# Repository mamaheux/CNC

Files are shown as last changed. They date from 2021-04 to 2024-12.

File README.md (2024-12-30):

# CNC
This is a project to learn how to create a 3-axis CNC router. It contains the mechanical, electrical and software designs.

## Folder Descriptions

### CAD
This folder contains the CAD files to build the CNC. It is built from aluminium extrusions and 3D printed parts.

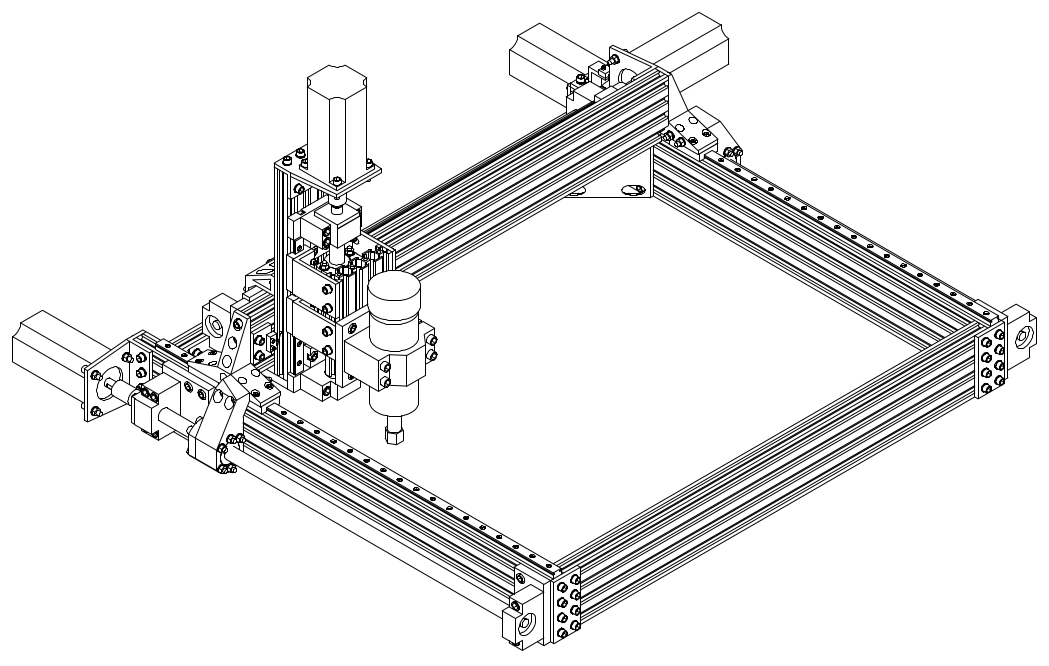
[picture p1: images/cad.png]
CAD


### control
This folder contains the graphical user interface for controlling the CNC from a computer.

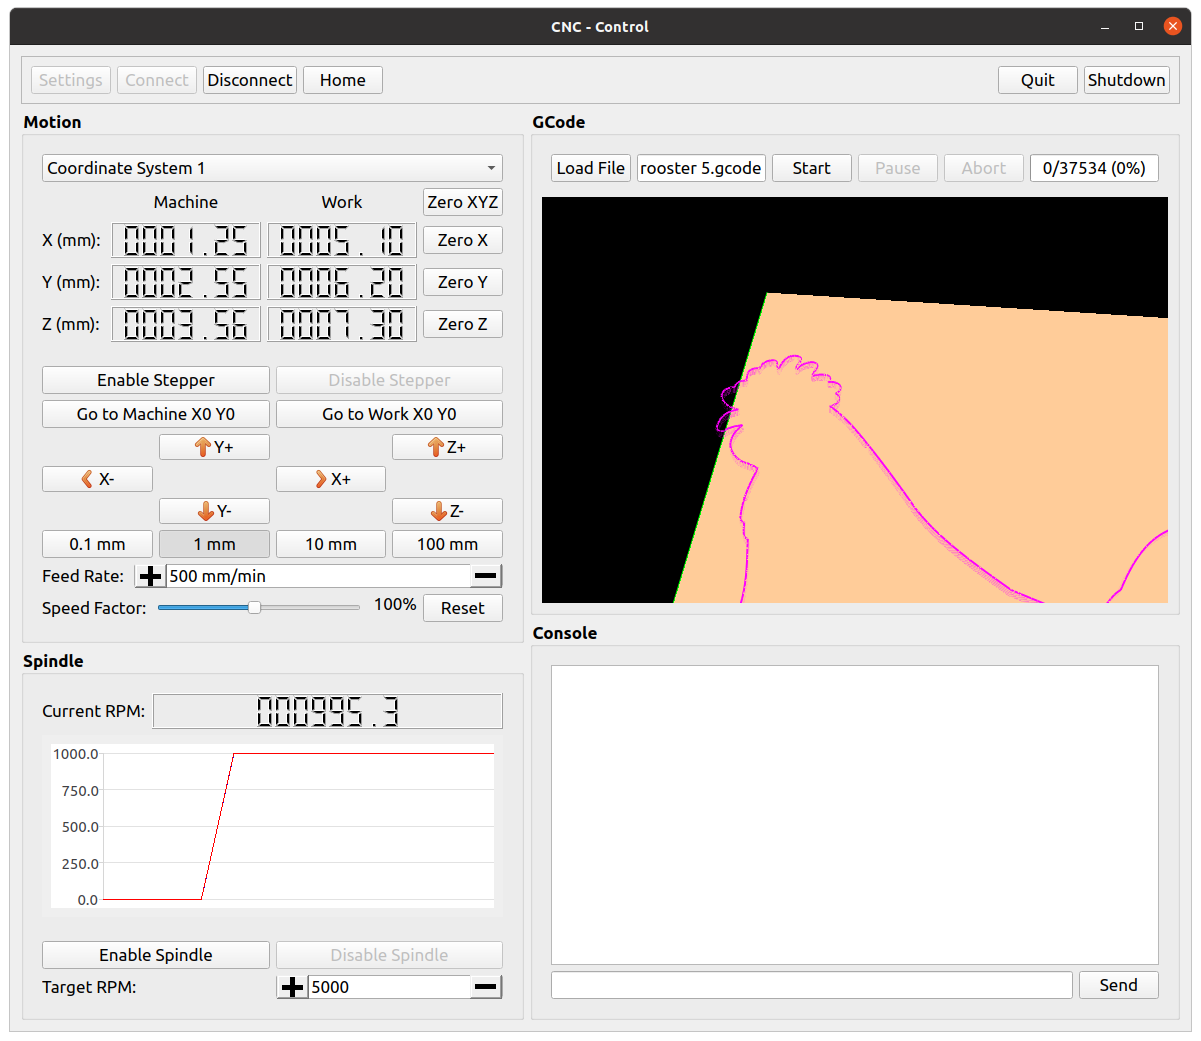
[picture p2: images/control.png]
Control


### electronics/teensy
This folder contains the PCB design of the board controlling the stepper drivers, endstops, and spindle drive.

### firmware
This folder contains the firmware that parses the G-code to control the spindle speed and the stepper motors using a trapezoidal velocity profile.

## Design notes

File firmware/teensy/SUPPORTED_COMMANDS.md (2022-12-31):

# Supported G-Codes

## G-Code Axis Names
- X
- Y
- Z
- A (not supported)
- B (not supported)
- C (not supported)
- E (not supported)
- U (not supported)
- V (not supported)
- W (not supported)

## Modal State
- Machine Coordinates
- Worskspace Coordinates (9)
- `G0` Feed Rate
- `G1`, `G2`, `G3` Feed Rate
- Global Offset (`G92`)

## Units
| Name | Units |
| --- | --- |
| Axis X, Y, Z | mm or in |
| Feedrate | mm or in per minute |
| Spindle Speed  | RPM |

## System Commands (GRBL)
| Name | Command | Handled | Tested |
| --- | --- | --- | --- |
| Homing | `$H` | Yes | Yes |

## G-Codes

| G-Code | Documentation | Parameters | Example | Handled | Tested |
| --- | --- | --- | --- | --- | --- |
| `G0` | [Link 1](https://smoothieware.org/g0), [Link 2](http://linuxcnc.org/docs/html/gcode/g-code.html#gcode:g0) | Axes, feedrate (mm/min), spindle speed | `G0 X5 F50` | Yes | Yes |
| `G1` | [Link 1](https://smoothieware.org/g1), [Link 2](http://linuxcnc.org/docs/html/gcode/g-code.html#gcode:g1) | Axes, feedrate (mm/min), spindle speed | `G1 X5 F50` | Yes | Yes |
| `G2` | [Link 1](https://smoothieware.org/g2), [Link 2](http://linuxcnc.org/docs/html/gcode/g-code.html#gcode:g2-g3) | Axes, center offsets (I, J, K) or radius (R), turn count (P), feedrate (mm/min), spindle speed | `G2 X5 Y5 I-5 J5 F10` | Yes | Yes |
| `G3` | [Link 1](https://smoothieware.org/g3), [Link 2](http://linuxcnc.org/docs/html/gcode/g-code.html#gcode:g2-g3) | Axes, center offsets (I, J, K) or radius (R), turn count (P), feedrate (mm/min), spindle speed | `G3 X5 Y5 I-5 J5 F10` | Yes | Yes |
| `G10 L2` | [Link](http://linuxcnc.org/docs/html/gcode/g-code.html#gcode:g10-l2) | Coordinate System (P), axes, R | `G10 L2 P2 X1 Y2` | Yes | Yes |
| `G10 L20`  | [Link](http://linuxcnc.org/docs/html/gcode/g-code.html#gcode:g10-l20) | Coordinate System (P), axes | `G10 L20 P3 X1` | Yes | Yes |
| `G17` | [Link 1](https://smoothieware.org/g17), [Link 2](http://linuxcnc.org/docs/html/gcode/g-code.html#gcode:g17-g19.1) | | `G17` | Yes | Yes |
| `G18` | [Link 1](https://smoothieware.org/g18), [Link 2](http://linuxcnc.org/docs/html/gcode/g-code.html#gcode:g17-g19.1) | | `G18` | Yes | Yes |
| `G19` | [Link 1](https://smoothieware.org/g19), [Link 2](http://linuxcnc.org/docs/html/gcode/g-code.html#gcode:g17-g19.1) | | `G19` | Yes | Yes |
| `G20` | [Link 1](https://smoothieware.org/g20), [Link 2](http://linuxcnc.org/docs/html/gcode/g-code.html#gcode:g20-g21) | | `G20` | Yes | Yes |
| `G21` | [Link 1](https://smoothieware.org/g21), [Link 2](http://linuxcnc.org/docs/html/gcode/g-code.html#gcode:g20-g21) | | `G21` | Yes | Yes |
| `G53` | [Link](http://linuxcnc.org/docs/html/gcode/g-code.html#gcode:g53) | G1 or G1 (modal commands are permitted) | `G53 G0 X0 Y0 Z0` | Yes | Yes |
| `G54-59.3` | [Link](http://linuxcnc.org/docs/html/gcode/g-code.html#gcode:g54-g59.3) | | `G54` | Yes | Yes |
| `G90` | [Link 1](https://smoothieware.org/g90), [Link 2](http://linuxcnc.org/docs/html/gcode/g-code.html#gcode:g90-g91) | | `G90` | Yes | Yes |
| `G90.1` | [Link 2](http://linuxcnc.org/docs/html/gcode/g-code.html#gcode:g90.1-g91.1) | | `G90.1` | Yes | Yes |
| `G91` | [Link 1](https://smoothieware.org/g91), [Link 2](http://linuxcnc.org/docs/html/gcode/g-code.html#gcode:g90-g91) | | `G91` | Yes | Yes |
| `G91.1` | [Link 2](http://linuxcnc.org/docs/html/gcode/g-code.html#gcode:g90.1-g91.1) | | `G91.1` | Yes | Yes |
| `G92` | [Link 1](https://smoothieware.org/g92), [Link 2](http://linuxcnc.org/docs/html/gcode/g-code.html#gcode:g92) | Axes (optional) | `G92 X1` | Yes | Yes |
| `G92.1` | [Link](http://linuxcnc.org/docs/html/gcode/g-code.html#gcode:g92.1-g92.2) | Axes (optional) | `G92.1` | Yes | Yes |

## Supported G-Code Parameter Names
- X
- Y
- Z
- F
- I
- J
- K
- S
- P
- R
- L

## M-Codes

| M-Code | Documentation | Parameters | Example | Handled | Tested |
| --- | --- | --- | --- | --- | --- |
| `M3` | [Link](https://smoothieware.org/m3) | Spindle Speed (S) | `M3 S500` | Yes | |
| `M5` | [Link](https://smoothieware.org/m5) | | `M5` | Yes | |
| `M17` | Enable all stepper motors. | | `M17` | Yes | Yes |
| `M18` | Disable all stepper motors. | | `M18` | Yes | Yes |
| `M20` | List all files. | | `M20` | Yes | Yes |
| `M23` | Select a G-Code file. | File path | `M23 file.gcode` | Yes | Yes |
| `M24` | Start or resume the selected file. | | `M24` | Yes | |
| `M25` | Pause the selected file. | | `M25` | Yes | |
| `M26` | Abort the selected file. | | `M26` | Yes | Yes |
| `M27` | Report the progress of the selected file (line count). | | `M27` | Yes | Yes |
| `M28` | Start to write the specified file. | File path | `M28 file.gcode` | Yes | Yes |
| `M29` | End to write the current file. | | `M29` | Yes | Yes |
| `M30` | Delete the specified file. | File path | `M30 file.gcode` | Yes | Yes |
| `M32` | Select a G-Code file and start the selected file. | File path | `M32 file.gcode` | Yes | |
| `M114` | Print the last requested position in the selected coordinate system | | `M114` | Yes | Yes |
| `M114.1` | Print the real time position in the selected coordinate system | | `M114.1` | Yes | Yes |
| `M114.2` | Print the last requested position in the machine coordinate system | | `M114.2` | Yes | Yes |
| `M114.3` | Print the real time position in the machine coordinate system | | `M114.3` | Yes | Yes |
| `M203` | Print the maximum feed rate values and set the maximum feed rate (mm/sec). | Feed rate (S) | `M203 S200` | Yes | Yes |
| `M204` | Print the acceleration values and set the acceleration (mm^2/sec). | Acceleration (S)  | `M204 S200` | Yes | Yes |
| `M220` | Print the speed factor and set the speed factor (percent). | Percent (S) | `M220 S25` | Yes | Yes |
| `M957` | Print the spindle speed (RPM) | | `M957` | Yes | Yes |
| `M958` | Print the spindle PID gain values and set the spindle PID gain values. | P, I, D | `M958 P0.1 I0.2` | Yes | Yes |

## Supported M-Code Parameter Names
- S
- File parameter
- P
- I
- D

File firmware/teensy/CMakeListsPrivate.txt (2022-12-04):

# !!! WARNING !!! AUTO-GENERATED FILE, PLEASE DO NOT MODIFY IT AND USE
# https://docs.platformio.org/page/projectconf/section_env_build.html#build-flags
#
# If you need to override existing CMake configuration or add extra,
# please create `CMakeListsUser.txt` in the root of project.
# The `CMakeListsUser.txt` will not be overwritten by PlatformIO.

set(CMAKE_CONFIGURATION_TYPES "teensy41;native;" CACHE STRING "Build Types reflect PlatformIO Environments" FORCE)

# Convert "Home Directory" that may contain unescaped backslashes on Windows

SET(CMAKE_C_COMPILER "$ENV{HOME}/.platformio/packages/toolchain-gccarmnoneeabi@1.50401.190816/bin/arm-none-eabi-gcc")
SET(CMAKE_CXX_COMPILER "$ENV{HOME}/.platformio/packages/toolchain-gccarmnoneeabi@1.50401.190816/bin/arm-none-eabi-g++")
SET(CMAKE_CXX_FLAGS "-fno-exceptions -felide-constructors -fno-rtti -std=gnu++14 -Wno-error=narrowing -fpermissive -fno-threadsafe-statics -Wall -ffunction-sections -fdata-sections -mthumb -mcpu=cortex-m7 -nostdlib -fsingle-precision-constant -mfloat-abi=hard -mfpu=fpv5-d16 -O2")
SET(CMAKE_C_FLAGS "-Wall -ffunction-sections -fdata-sections -mthumb -mcpu=cortex-m7 -nostdlib -fsingle-precision-constant -mfloat-abi=hard -mfpu=fpv5-d16 -O2")

set(CMAKE_CXX_STANDARD 14)

if (CMAKE_BUILD_TYPE MATCHES "teensy41")
    add_definitions(-DPLATFORMIO=60105)
    add_definitions(-D__IMXRT1062__)
    add_definitions(-DARDUINO_TEENSY41)
    add_definitions(-DUSB_SERIAL)
    add_definitions(-DARDUINO=10805)
    add_definitions(-DTEENSYDUINO=154)
    add_definitions(-DCORE_TEENSY)
    add_definitions(-DF_CPU=600000000)
    add_definitions(-DLAYOUT_US_ENGLISH)

    include_directories("${CMAKE_CURRENT_LIST_DIR}/include")
    include_directories("${CMAKE_CURRENT_LIST_DIR}/src")
    include_directories("${CMAKE_CURRENT_LIST_DIR}/lib/cnc/include")
    include_directories("${CMAKE_CURRENT_LIST_DIR}/lib/cnc/src")
    include_directories("$ENV{HOME}/.platformio/packages/framework-arduinoteensy/libraries/SD/src")
    include_directories("$ENV{HOME}/.platformio/packages/framework-arduinoteensy/libraries/SdFat/src")
    include_directories("$ENV{HOME}/.platformio/packages/framework-arduinoteensy/libraries/SPI")
    include_directories("${CMAKE_CURRENT_LIST_DIR}/.pio/libdeps/teensy41/optional/include")
    include_directories("${CMAKE_CURRENT_LIST_DIR}/.pio/libdeps/teensy41/optional")
    include_directories("$ENV{HOME}/.platformio/packages/framework-arduinoteensy/cores/teensy4")
    include_directories("${CMAKE_CURRENT_LIST_DIR}/.pio/libdeps/teensy41/SD")
    include_directories("$ENV{HOME}/.platformio/packages/framework-arduinoteensy/libraries/ADC")
    include_directories("$ENV{HOME}/.platformio/packages/framework-arduinoteensy/libraries/AccelStepper/src")
    include_directories("$ENV{HOME}/.platformio/packages/framework-arduinoteensy/libraries/Adafruit_NeoPixel")
    include_directories("$ENV{HOME}/.platformio/packages/framework-arduinoteensy/libraries/Adafruit_STMPE610")
    include_directories("$ENV{HOME}/.platformio/packages/framework-arduinoteensy/libraries/Adafruit_VS1053")
    include_directories("$ENV{HOME}/.platformio/packages/framework-arduinoteensy/libraries/Adafruit_nRF8001")
    include_directories("$ENV{HOME}/.platformio/packages/framework-arduinoteensy/libraries/Adafruit_nRF8001/utility")
    include_directories("$ENV{HOME}/.platformio/packages/framework-arduinoteensy/libraries/AltSoftSerial")
    include_directories("$ENV{HOME}/.platformio/packages/framework-arduinoteensy/libraries/Artnet")
    include_directories("$ENV{HOME}/.platformio/packages/framework-arduinoteensy/libraries/Audio")
    include_directories("$ENV{HOME}/.platformio/packages/framework-arduinoteensy/libraries/Audio/utility")
    include_directories("$ENV{HOME}/.platformio/packages/framework-arduinoteensy/libraries/Bounce")
    include_directories("$ENV{HOME}/.platformio/packages/framework-arduinoteensy/libraries/Bounce2/src")
    include_directories("$ENV{HOME}/.platformio/packages/framework-arduinoteensy/libraries/CapacitiveSensor")
    include_directories("$ENV{HOME}/.platformio/packages/framework-arduinoteensy/libraries/CryptoAccel/src")
    include_directories("$ENV{HOME}/.platformio/packages/framework-arduinoteensy/libraries/DS1307RTC")
    include_directories("$ENV{HOME}/.platformio/packages/framework-arduinoteensy/libraries/DmxSimple")
    include_directories("$ENV{HOME}/.platformio/packages/framework-arduinoteensy/libraries/DogLcd")
    include_directories("$ENV{HOME}/.platformio/packages/framework-arduinoteensy/libraries/EEPROM")
    include_directories("$ENV{HOME}/.platformio/packages/framework-arduinoteensy/libraries/EasyTransfer")
    include_directories("$ENV{HOME}/.platformio/packages/framework-arduinoteensy/libraries/EasyTransferI2C")
    include_directories("$ENV{HOME}/.platformio/packages/framework-arduinoteensy/libraries/Encoder")
    include_directories("$ENV{HOME}/.platformio/packages/framework-arduinoteensy/libraries/Encoder/utility")
    include_directories("$ENV{HOME}/.platformio/packages/framework-arduinoteensy/libraries/Entropy")
    include_directories("$ENV{HOME}/.platformio/packages/framework-arduinoteensy/libraries/Ethernet/src")
    include_directories("$ENV{HOME}/.platformio/packages/framework-arduinoteensy/libraries/FNET/src")
    include_directories("$ENV{HOME}/.platformio/packages/framework-arduinoteensy/libraries/FastCRC")
    include_directories("$ENV{HOME}/.platformio/packages/framework-arduinoteensy/libraries/FastLED")
    include_directories("$ENV{HOME}/.platformio/packages/framework-arduinoteensy/libraries/FlexCAN")
    include_directories("$ENV{HOME}/.platformio/packages/framework-arduinoteensy/libraries/FlexCAN_T4")
    include_directories("$ENV{HOME}/.platformio/packages/framework-arduinoteensy/libraries/FlexIO_t4/src")
    include_directories("$ENV{HOME}/.platformio/packages/framework-arduinoteensy/libraries/FlexiTimer2")
    include_directories("$ENV{HOME}/.platformio/packages/framework-arduinoteensy/libraries/FreqCount")
    include_directories("$ENV{HOME}/.platformio/packages/framework-arduinoteensy/libraries/FreqMeasure")
    include_directories("$ENV{HOME}/.platformio/packages/framework-arduinoteensy/libraries/FreqMeasureMulti")
    include_directories("$ENV{HOME}/.platformio/packages/framework-arduinoteensy/libraries/FrequencyTimer2")
    include_directories("$ENV{HOME}/.platformio/packages/framework-arduinoteensy/libraries/ILI9341_t3")
    include_directories("$ENV{HOME}/.platformio/packages/framework-arduinoteensy/libraries/ILI9488_t3/src")
    include_directories("$ENV{HOME}/.platformio/packages/framework-arduinoteensy/libraries/IRremote")
    include_directories("$ENV{HOME}/.platformio/packages/framework-arduinoteensy/libraries/Keypad/src")
    include_directories("$ENV{HOME}/.platformio/packages/framework-arduinoteensy/libraries/LedControl/src")
    include_directories("$ENV{HOME}/.platformio/packages/framework-arduinoteensy/libraries/LedDisplay")
    include_directories("$ENV{HOME}/.platformio/packages/framework-arduinoteensy/libraries/LiquidCrystal/src")
    include_directories("$ENV{HOME}/.platformio/packages/framework-arduinoteensy/libraries/LiquidCrystalFast")
    include_directories("$ENV{HOME}/.platformio/packages/framework-arduinoteensy/libraries/LittleFS/src")
    include_directories("$ENV{HOME}/.platformio/packages/framework-arduinoteensy/libraries/LowPower")
    include_directories("$ENV{HOME}/.platformio/packages/framework-arduinoteensy/libraries/MFRC522/src")
    include_directories("$ENV{HOME}/.platformio/packages/framework-arduinoteensy/libraries/MIDI/src")
    include_directories("$ENV{HOME}/.platformio/packages/framework-arduinoteensy/libraries/Metro")
    include_directories("$ENV{HOME}/.platformio/packages/framework-arduinoteensy/libraries/MsTimer2")
    include_directories("$ENV{HOME}/.platformio/packages/framework-arduinoteensy/libraries/NXPMotionSense")
    include_directories("$ENV{HOME}/.platformio/packages/framework-arduinoteensy/libraries/NXPMotionSense/utility")
    include_directories("$ENV{HOME}/.platformio/packages/framework-arduinoteensy/libraries/NativeEthernet/src")
    include_directories("$ENV{HOME}/.platformio/packages/framework-arduinoteensy/libraries/OSC")
    include_directories("$ENV{HOME}/.platformio/packages/framework-arduinoteensy/libraries/OctoWS2811")
    include_directories("$ENV{HOME}/.platformio/packages/framework-arduinoteensy/libraries/OneWire")
    include_directories("$ENV{HOME}/.platformio/packages/framework-arduinoteensy/libraries/PS2Keyboard")
    include_directories("$ENV{HOME}/.platformio/packages/framework-arduinoteensy/libraries/PS2Keyboard/utility")
    include_directories("$ENV{HOME}/.platformio/packages/framework-arduinoteensy/libraries/PWMServo")
    include_directories("$ENV{HOME}/.platformio/packages/framework-arduinoteensy/libraries/Ping")
    include_directories("$ENV{HOME}/.platformio/packages/framework-arduinoteensy/libraries/PulsePosition")
    include_directories("$ENV{HOME}/.platformio/packages/framework-arduinoteensy/libraries/QuadEncoder")
    include_directories("$ENV{HOME}/.platformio/packages/framework-arduinoteensy/libraries/RA8875")
    include_directories("$ENV{HOME}/.platformio/packages/framework-arduinoteensy/libraries/RadioHead")
    include_directories("$ENV{HOME}/.platformio/packages/framework-arduinoteensy/libraries/ResponsiveAnalogRead/src")
    include_directories("$ENV{HOME}/.platformio/packages/framework-arduinoteensy/libraries/SPIFlash")
    include_directories("$ENV{HOME}/.platformio/packages/framework-arduinoteensy/libraries/ST7735_t3")
    include_directories("$ENV{HOME}/.platformio/packages/framework-arduinoteensy/libraries/SerialFlash")
    include_directories("$ENV{HOME}/.platformio/packages/framework-arduinoteensy/libraries/Servo")
    include_directories("$ENV{HOME}/.platformio/packages/framework-arduinoteensy/libraries/ShiftPWM")
    include_directories("$ENV{HOME}/.platformio/packages/framework-arduinoteensy/libraries/Snooze/src")
    include_directories("$ENV{HOME}/.platformio/packages/framework-arduinoteensy/libraries/SoftPWM")
    include_directories("$ENV{HOME}/.platformio/packages/framework-arduinoteensy/libraries/SoftwareSerial")
    include_directories("$ENV{HOME}/.platformio/packages/framework-arduinoteensy/libraries/TFT_ILI9163C")
    include_directories("$ENV{HOME}/.platformio/packages/framework-arduinoteensy/libraries/Talkie")
    include_directories("$ENV{HOME}/.platformio/packages/framework-arduinoteensy/libraries/TeensyThreads")
    include_directories("$ENV{HOME}/.platformio/packages/framework-arduinoteensy/libraries/Time")
    include_directories("$ENV{HOME}/.platformio/packages/framework-arduinoteensy/libraries/TimeAlarms")
    include_directories("$ENV{HOME}/.platformio/packages/framework-arduinoteensy/libraries/TimerOne")
    include_directories("$ENV{HOME}/.platformio/packages/framework-arduinoteensy/libraries/TimerThree")
    include_directories("$ENV{HOME}/.platformio/packages/framework-arduinoteensy/libraries/TinyGPS")
    include_directories("$ENV{HOME}/.platformio/packages/framework-arduinoteensy/libraries/Tlc5940")
    include_directories("$ENV{HOME}/.platformio/packages/framework-arduinoteensy/libraries/TouchScreen")
    include_directories("$ENV{HOME}/.platformio/packages/framework-arduinoteensy/libraries/USBHost_t36")
    include_directories("$ENV{HOME}/.platformio/packages/framework-arduinoteensy/libraries/USBHost_t36/utility")
    include_directories("$ENV{HOME}/.platformio/packages/framework-arduinoteensy/libraries/UTFT")
    include_directories("$ENV{HOME}/.platformio/packages/framework-arduinoteensy/libraries/VirtualWire")
    include_directories("$ENV{HOME}/.platformio/packages/framework-arduinoteensy/libraries/WS2812Serial")
    include_directories("$ENV{HOME}/.platformio/packages/framework-arduinoteensy/libraries/Wire")
    include_directories("$ENV{HOME}/.platformio/packages/framework-arduinoteensy/libraries/Wire/utility")
    include_directories("$ENV{HOME}/.platformio/packages/framework-arduinoteensy/libraries/XBee")
    include_directories("$ENV{HOME}/.platformio/packages/framework-arduinoteensy/libraries/XPT2046_Touchscreen")
    include_directories("$ENV{HOME}/.platformio/packages/framework-arduinoteensy/libraries/i2c_t3")
    include_directories("$ENV{HOME}/.platformio/packages/framework-arduinoteensy/libraries/ks0108")
    include_directories("$ENV{HOME}/.platformio/packages/framework-arduinoteensy/libraries/ssd1351")
    include_directories("$ENV{HOME}/.platformio/packages/framework-arduinoteensy/libraries/x10")
    include_directories("$ENV{HOME}/.platformio/packages/toolchain-gccarmnoneeabi@1.50401.190816/arm-none-eabi/include/c++/5.4.1")
    include_directories("$ENV{HOME}/.platformio/packages/toolchain-gccarmnoneeabi@1.50401.190816/arm-none-eabi/include/c++/5.4.1/arm-none-eabi")
    include_directories("$ENV{HOME}/.platformio/packages/toolchain-gccarmnoneeabi@1.50401.190816/lib/gcc/arm-none-eabi/5.4.1/include")
    include_directories("$ENV{HOME}/.platformio/packages/toolchain-gccarmnoneeabi@1.50401.190816/lib/gcc/arm-none-eabi/5.4.1/include-fixed")
    include_directories("$ENV{HOME}/.platformio/packages/toolchain-gccarmnoneeabi@1.50401.190816/arm-none-eabi/include")

    FILE(GLOB_RECURSE EXTRA_LIB_SOURCES
        ${CMAKE_CURRENT_LIST_DIR}/.pio/libdeps/teensy41/*.*
    )
endif()

if (CMAKE_BUILD_TYPE MATCHES "native")
    add_definitions(-DPLATFORMIO=60105)

    include_directories("${CMAKE_CURRENT_LIST_DIR}/include")
    include_directories("${CMAKE_CURRENT_LIST_DIR}/src")
    include_directories("${CMAKE_CURRENT_LIST_DIR}/lib/cnc/include")
    include_directories("${CMAKE_CURRENT_LIST_DIR}/lib/cnc/src")
    include_directories("${CMAKE_CURRENT_LIST_DIR}/.pio/libdeps/native/optional/include")
    include_directories("${CMAKE_CURRENT_LIST_DIR}/.pio/libdeps/native/optional")
    include_directories("${CMAKE_CURRENT_LIST_DIR}/.pio/libdeps/native/Unity/src")

    FILE(GLOB_RECURSE EXTRA_LIB_SOURCES
        ${CMAKE_CURRENT_LIST_DIR}/.pio/libdeps/native/*.*
    )
endif()

FILE(GLOB_RECURSE SRC_LIST
    ${CMAKE_CURRENT_LIST_DIR}/src/*.*
    ${CMAKE_CURRENT_LIST_DIR}/lib/*.*
    ${CMAKE_CURRENT_LIST_DIR}/test/*.*
)

list(APPEND SRC_LIST ${EXTRA_LIB_SOURCES})

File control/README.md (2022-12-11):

# control
This is a Qt interface to control the CNC.

## Dependencies
```bash
sudo apt install qtbase5-dev qtchooser qt5-qmake qtbase5-dev-tools libqt5charts5* libqt5serialport5* libqt5opengl5* \ 
    mesa-common-dev libglu1-mesa-dev freeglut3-dev libgl-dev
```

## Linux Setup
Execute the following command `sudo visudo` and add the following line at the end.
```
%sudo ALL=(ALL) NOPASSWD: /sbin/poweroff, /sbin/reboot, /sbin/shutdown
```

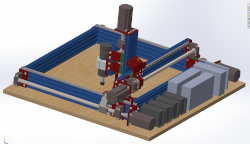
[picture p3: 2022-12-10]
control/resources/images/cnc.png

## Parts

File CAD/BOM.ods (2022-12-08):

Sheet: shop
Description | Links |  |  | Quantity
Stepper Nema 23 2.8A | ici (https://www.banggood.com/Nema-23-CNC-Stepper-Motor-DC-24-48V-3Nm-Stepper-Motor-For-CNC-Parts-p-1162662.html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) | ici (https://www.amazon.ca/-/fr/Moteur-Longueur-couple-élevé-imprimante/dp/B074W8N47K) | ici (https://www.amazon.ca/-/fr/moteurs-couple-élevé-longueur-imprimante/dp/B075KFSSP7) | 4
Stepper Driver 4.2A | ici (https://www.banggood.com/HANPOSE-DSP-Digital-DM542-128-Stepper-Motor-Driver-4_2A-DC9-42V-For-Nema-172334-Stepper-Motor-CNC-Engraving-Machine-p-1565166.html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) | ici (https://www.amazon.ca/-/fr/Pilote-moteur-phases-conduite-moteurs/dp/B07RVHVJW5?__mk_fr_CA=ÅMÅŽÕÑ&s=industrial) | ici (https://www.banggood.com/HANPOSE-TB6600-Stepper-Motor-Driver-4A-DC9-42V-For-Nema-17-or-23-or-34-Stepper-Motor-CNC-Engraving-Machine-p-1415418.html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) | 4
24V PSU | ici (https://www.banggood.com/Geekcreit-AC-110-240V-Input-To-DC-24V-17A-400W-Switching-Power-Supply-Driver-Board-p-1272112.html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) | ici (https://www.amazon.ca/Alimentation-Adaptateur-convertisseur-commutation-Transformateur/dp/B07TWW8Q73) |  | 1
Spindle + PSU + Controller | ici (https://www.banggood.com/Machifit-ER11-or-ER16-Chuck-CNC-500W-Brushless-Spindle-Motor-With-55mm-Clamps-and-Power-Supply-Speed-Governor-Speed-Control-Device-p-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) |  |  | 1
ER16 chuck collet | ici (https://www.banggood.com/ER16-10pcs-1-10mm-Spring-Collet-CNC-Carving-Machine-Milling-Chuck-Collet-Lathe-Tool-p-1199297.html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) |  |  | 1
Cable tray | ici (https://www.banggood.com/10-x-20mm-Plastic-Cable-Drag-Chain-Wire-Carrier-Length-1000mm-With-End-Connectors-For-CNC-p-995514.html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) |  |  | 2
XY ball screw | ici (https://www.banggood.com/600mm-SFU1605-Ball-Screw-with-BK12-BF12-Supports-and-6_35x10mm-Coupler-for-CNC-p-1054578.html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) |  |  | 3
Z ball screw | ici (https://www.banggood.com/SFU1605-Ball-Screw-Length-250mm-with-1-Set-BKBF12-Supports-and-6_35mm-x-10mm-Coupler-for-CNC-p-1060449.html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) |  |  | 1
X linear guide | ici (https://www.banggood.com/Machifit-MGN12-100-1000mm-Linear-Rail-Guide-with-MGN12H-Linear-Sliding-Guide-Block-CNC-Parts-p-1156260.html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) |  |  | 2
Y linear guide | ici (https://www.banggood.com/Machifit-MGN12-100-1000mm-Linear-Rail-Guide-with-MGN12H-Linear-Sliding-Guide-Block-CNC-Parts-p-1156260.html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) |  |  | 2
Z linear guide | ici (https://www.banggood.com/Machifit-MGN12-100-1000mm-Linear-Rail-Guide-with-MGN12H-Linear-Sliding-Guide-Block-CNC-Parts-p-1156260.html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) |  |  | 2
Linear guide carrier | ici (https://www.banggood.com/Machifit-MGN12H-Linear-Rail-Block-for-MGN12-Linear-Rail-Guide-CNC-Tool-p-1186173.html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) |  |  | 6
Aluminium extrusion 2080 | ici (https://www.banggood.com/Machifit-200-1000mm-Black-2080-V-Slot-Aluminum-Profile-Extrusion-Frame-for-CNC-Tool-DIY-p-1342019.html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) |  |  | 6
Controller | ici (https://www.amazon.ca/-/fr/gp/product/B082PS64QW/ref=ppx_od_dt_b_asin_title_s00?ie=UTF8&psc=1) |  |  | 1
Milling end | ici (https://www.banggood.com/Drillpro-8pcs-2-12mm-4-Flutes-Carbide-End-Mill-Set-Tungsten-Steel-Milling-Cutter-CNC-Tool-p-1139712.html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) | ici (https://www.banggood.com/7pcs-1-8mm-Solid-Carbide-Straight-End-Mill-4-Flute-Milling-Cutter-CNC-Tool-p-1665306.html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)
M2.5x10mm |  |  |  | 6
M3x8mm |  |  |  | 148
M3x25mm |  |  |  | 4
M3 T nut (50) | ici (https://www.banggood.com/Drillpro-50pcs-M3-T-Sliding-Nut-Zinc-Plated-Carbon-Steel-T-Sliding-Nut-for-2020-Aluminum-Profile-p-1081131.html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) |  |  | 3
M3 washer |  |  |  | 45
M5x10mm |  |  |  | 128
M5x20mm |  |  |  | 16
M5x30mm |  |  |  | 4
M5x50mm |  |  |  | 22
M5 T nut (100) | ici (https://www.banggood.com/Drillpro-100pcs-M5-Hammer-Nut-Nickel-Plated-Carbon-Steel-Aluminum-Connector-T-Fastener-Sliding-Nut-p-1048442.html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) |  |  | 1
M5 nut |  |  |  | 38
M5 washer |  |  |  | 170
M6x40mm |  |  |  | 24
M6x70mm |  |  |  | 4
M6 nut |  |  |  | 28
M6 washer |  |  |  | 28
Touchscreen | ici (https://www.amazon.com/13-3inch-HDMI-LCD-case-Resolution/dp/B077PTMPSX) |  |  | 1
Raspberry pi 4 | ici (https://www.buyapi.ca/product/raspberry-pi-4-model-b-4gb/) |  |  | 1

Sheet: 3D_print
File | Quantity | Printed Quantity | Total quantity | 35
spindle frame support | 4 | 4 | Printed quantity | 35
spindle mount spacer | 1 | 1
X frame BF12 spacer | 2 | 2
X frame BK12 spacer | 2 | 2
X frame corner plate | 2 | 2
X frame corner | 2 | 2
X frame screw support left | 1 | 1
X frame screw support right | 1 | 1
X limit switch support | 1 | 1
XZ frame motor support | 3 | 3
Y frame screw support | 1 | 1
Y frame support left | 1 | 1
Y frame support right | 1 | 1
Y limit switch support | 1 | 1
YZ frame BF12 spacer | 2 | 2
YZ frame BK12 spacer | 2 | 2
Z frame screw support | 1 | 1
Z frame support bottom | 1 | 1
Z frame support top | 1 | 1
Z limit switch support | 1 | 1
table support | 4 | 4

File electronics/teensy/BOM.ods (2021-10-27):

Item | Qty | Reference(s) | Value | Link
1 | 1 | C1 | 33µF/35V | https://www.digikey.ca/en/products/detail/nichicon/UPX1V330MPD1TD/4320154
2 | 1 | C2 | 10µF/10V/Low ESL | https://www.digikey.ca/en/products/detail/tdk-corporation/C2012X7R1A106M125AC/2733027
3 | 4 | C3, C9, C10, C23 | 1µF/35V | https://www.digikey.ca/en/products/detail/taiyo-yuden/GMK212BJ105KGHT/4157463
4 | 1 | C4 | 22µF/10V/Low ESL | https://www.digikey.ca/en/products/detail/tdk-corporation/C2012X5R1A226M085AC/2733098
5 | 1 | C5 | 0.33µF | https://www.digikey.ca/en/products/detail/tdk-corporation/CGA4J2X7R1H334K125AA/2443162
6 | 13 | C6, C11, C12, C13, C14, C15, C16, C17, C18, C19, C20, C22, C25 | 0.1µF/25V | https://www.digikey.ca/en/products/detail/kyocera-avx/08053C104KAT2A/1116281
7 | 1 | C7 | 330µF/10V | https://www.digikey.ca/en/products/detail/nichicon/UKL1A331MPD1TD/4318088
8 | 1 | C8 | 2.2µF/35V | https://www.digikey.ca/en/products/detail/tdk-corporation/C2012X5R1V225K085AB/3951660
9 | 1 | C21 | 47nF/21V | https://www.digikey.ca/en/products/detail/taiyo-yuden/TMK212B7473KD-T/930632
10 | 1 | C24 | 4700pF | https://www.digikey.ca/en/products/detail/samsung-electro-mechanics/CL21C472JAFNNNE/3888659
11 | 2 | D1, D2 | B340AE-13 | https://www.digikey.ca/en/products/detail/diodes-incorporated/B340AE-13/7352831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
12 | 1 | D3 | ORANGE | https://www.digikey.ca/en/products/detail/osram-opto-semiconductors-inc/LO-R976-PS-1/1227955
13 | 1 | D4 | GREEN | https://www.digikey.ca/en/products/detail/lite-on-inc/LTST-C170KGKT/386777
14 | 1 | D5 | BLUE | https://www.digikey.ca/en/products/detail/lite-on-inc/LTST-C170TBKT/388527
15 | 1 | D6 | RED | https://www.digikey.ca/en/products/detail/lite-on-inc/LTST-C171KRKT/386801
16 | 1 | J1 | Vin 24V | https://www.digikey.ca/en/products/detail/adam-tech/EBWA-02-B/9830632?s=N4IgTCBcDaIKICEDqBBAtABjGhIC6AvkA
17 | 1 | J2 | Vout 5V | Ebay – JST XH
18 | 1 | J3 | Vout 3.3V | Ebay – JST XH
19 | 1 | J4 | X_MIN | Ebay – JST XH
20 | 1 | J5 | Y_MIN | Ebay – JST XH
21 | 1 | J6 | Z_MIN | Ebay – JST XH
22 | 1 | J7 | OTHER 1 | Ebay – JST XH
23 | 1 | J8 | X_MAX | Ebay – JST XH
24 | 1 | J9 | Y_MAX | Ebay – JST XH
25 | 1 | J10 | Z_MAX | Ebay – JST XH
26 | 1 | J11 | OTHER_2 | Ebay – JST XH
27 | 3 | J12, J14, J15 | Stepper X1 | Ebay – JST XH
28 | 1 | J13 | Stepper X2 | Ebay – JST XH
29 | 2 | J16, J20 | DC Motor Vin 24V | https://www.digikey.ca/en/products/detail/adam-tech/EBWA-02-B/9830632?s=N4IgTCBcDaIKICEDqBBAtABjGhIC6AvkA
30 | 1 | J17 | Cetus_J1B1211CCD | https://www.pjrc.com/store/ethernet_kit.html
31 | 2 | J18, J21 | DC Motor | https://www.digikey.ca/en/products/detail/adam-tech/EBWA-02-B/9830632?s=N4IgTCBcDaIKICEDqBBAtABjGhIC6AvkA
32 | 1 | J22 | SPINDLE_BLDC_CONTROLLER | Ebay – JST XH
33 | 1 | J23 | USB_B | Ebay – USB-B
34 | 2 | J24, J25 | EXT | Ebay – JST XH
35 | 1 | L1 | 68µH/Sumida CDRH104R-680MC | https://www.digikey.ca/product-detail/en/sumida-america-components-inc/CDRH104RNP-680NC/308-2170-1-ND/3946461
36 | 2 | Q1, Q3 | TK1R4S04PB | https://www.digikey.ca/en/products/detail/toshiba-semiconductor-and-storage/TK1R4S04PB-LXHQ/12154999
37 | 1 | Q4 | SI2301CDS-T1-E3 | https://www.digikey.ca/en/products/detail/vishay-siliconix/SI2301CDS-T1-E3/2622018
38 | 1 | R1 | 3.01k | Ebay – Kit 0805
39 | 1 | R2 | 976 | Ebay – Kit 0805
40 | 24 | R3, R4, R5, R6, R7, R8, R9, R10, R11, R12, R13, R14, R15, R16, R17, R18, R45, R47, R48, R57, R58, R66 | 10k | https://www.digikey.ca/en/products/detail/koa-speer-electronics-inc/SG73S2ATTD103J/10279997
41 | 18 | R19, R20, R21, R22, R27, R28, R29, R30, R35, R36, R37, R38, R43, R46, R51, R55, R56, R59 | 1k | https://www.digikey.ca/en/products/detail/stackpole-electronics-inc/RNCP0805FTD1K00/2240229
42 | 12 | R23, R24, R25, R26, R31, R32, R33, R34, R39, R40, R41, R42 | 1.82k/0.5W | https://www.digikey.ca/en/products/detail/stackpole-electronics-inc/RNCP1206FTD1K82/2240344
43 | 1 | R52 | 2.2k | Ebay – Kit 0805
44 | 1 | R53 | 47k | Ebay – Kit 0805
45 | 2 | R54, R67 | 100k | Ebay – Kit 0805
46 | 2 | R60, R61 | 24 | Ebay – Kit 0805
47 | 1 | R62 | 174 | Ebay – Kit 0805
48 | 2 | R63, R65 | 150 | Ebay – Kit 0805
49 | 1 | R64 | 30.1 | Ebay – Kit 0805
50 | 1 | R68 | 0.1µF/25V | https://www.digikey.ca/en/products/detail/stackpole-electronics-inc/RMCF1206ZT0R00/1756906
51 | 8 | RV1, RV2, RV3, RV4, RV5, RV6, RV7, RV8 | VC080503A100DP | https://www.digikey.ca/en/products/detail/kyocera-avx/VC080503A100DP/684850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
52 | 1 | U1 | MIC4684 | Sample
53 | 1 | U2 | AP7354-33W5-7 | https://www.digikey.ca/en/products/detail/diodes-incorporated/AP7354-33W5-7/9554534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
54 | 1 | U3 | AZ1117IH-3.3TRG1 | https://www.digikey.ca/en/products/detail/diodes-incorporated/AZ1117IH-3-3TRG1/5699672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
55 | 2 | U4, U5 | SN74LVC14ADRG3 | https://www.digikey.ca/en/products/detail/texas-instruments/SN74LVC14ADRG3/2421075
56 | 9 | U6, U7, U8, U9, U10, U11, U12, U13, U15 | MOCD217R2M | https://www.digikey.ca/en/products/detail/onsemi/MOCD217R2M/402226
57 | 1 | U14 | TS912 | https://www.digikey.ca/en/products/detail/stmicroelectronics/TS912IDT/1040339
58 | 1 | U17 | CY7C64225 | https://www.digikey.ca/en/products/detail/cypress-semiconductor-corp/CY7C64225-28PVXC/3507932
59 | 1 | U18 | LM810M3-4.63 | https://www.digikey.ca/en/products/detail/texas-instruments/LM810M3-4-63-NOPB/364278
60 | 1 | U19 | Teensy_4.1 | https://www.pjrc.com/store/teensy41.html
61 | 1 | U19 | Header | https://www.digikey.ca/en/products/detail/samtec-inc/SQT-103-01-L-D/1108681

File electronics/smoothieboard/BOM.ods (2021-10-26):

Item | Qty | Reference(s) | Value | Link
1 | 1 | C1 | 4700pF | https://www.digikey.ca/en/products/detail/samsung-electro-mechanics/CL21B472KBANNNC/3886813
2 | 4 | C2 C15, C23, C26 | 1µF/20V | https://www.digikey.ca/en/products/detail/samsung-electro-mechanics/CL21B105KBFNNNG/3894467
3 | 2 | C3, C9 | 1000µF/20V | https://www.digikey.ca/en/products/detail/rubycon/25PX1000MEFCT810X16/3134540
4 | 2 | C4, C6 | 18pF/20V | https://www.digikey.ca/en/products/detail/kemet/C0805C180M3HAC7800/7949065
5 | 1 | C7 | 2.2µF/20V | https://www.digikey.ca/en/products/detail/samsung-electro-mechanics/CL21A225KAFNNNG/3894427
6 | 2 | C8, C27 | 10µF/20V | https://www.digikey.ca/en/products/detail/murata-electronics/GRM21BC81D106KE51L/5027585
7 | 1 | C11 | 10pF/20V | https://www.digikey.ca/en/products/detail/samsung-electro-mechanics/CL21C100CBANNNC/3888219
8 | 1 | C13 | 47nF/20V | https://www.digikey.ca/en/products/detail/samsung-electro-mechanics/CL21B473KCCWPNC/5961299
9 | 14 | C5, C14, C16, C17, C18, C19, C20, C21, C22, C28, C29, C30, C31, C32, C33 | 0.1µF/20V | https://www.digikey.ca/en/products/detail/samsung-electro-mechanics/CL21B104KBCNNNC/3886661
10 | 2 | C24, C25 | 12pF/AC | https://www.digikey.ca/en/products/detail/yageo/CC0805FRNPO9BN120/5883925
11 | 3 | D1, D2, D3 | S1B-13-F | https://www.digikey.ca/en/products/detail/diodes-incorporated/S1B-13-F/725026
13 | 1 | J1 | 5V | https://www.digikey.ca/en/products/detail/adam-tech/EBWA-02-B/9830632
14 | 1 | J2 | USB_B | https://www.digikey.ca/en/products/detail/amphenol-icc-fci/61729-0010BLF/1001353
15 | 19 | J4, J6, J8, J10, J11, J12, J13, J14, J15, J16, J17, J18, J19, J21, J22, J24, J25, J26, J28, J29 | JST* | Ebay – JST
16 | 1 | J23 | JTAG | https://www.digikey.ca/en/products/detail/sullins-connector-solutions/SBH11-PBPC-D10-ST-BK/1990065
17 | 1 | J33 | MICROSD_CARD | https://www.digikey.ca/en/products/detail/hirose-electric-co-ltd/DM3D-SF/1786510
18 | 1 | J34 | ETHERNET | https://www.digikey.ca/en/products/detail/molex/0901301112/760948
19 | 1 | JP1 | 5V
20 | 3 | JP1, JP11, JP12 | Jumper_3_Open | https://www.digikey.ca/en/products/detail/sullins-connector-solutions/QPC02SXGN-RC/2618262
21 | 1 | L1 | 10 µH | https://www.digikey.ca/en/products/detail/tdk-corporation/MLZ2012M100WT000/2465153
22 | 1 | Q6 | 2N7002-7-F | https://www.digikey.ca/en/products/detail/diodes-incorporated/2N7002-7-F/717681
23 | 1 | Q8 | BSS84 | https://www.digikey.ca/en/products/detail/on-semiconductor/BSS84/244213
24 | 2 | R1, R2 | 33 | Ebay – Kit
25 | 1 | R39 | 200 | Ebay – Kit
26 | 18 | R4, R6, R8, R13, R15, R17, R22, R24, R26, R32, R33, R36, R40, R42, R44, R46, R48, R50 | 1k | Ebay – Kit
27 | 9 | R9, R10, R11, R18, R19, R20, R27, R28, R29 | 1.82k/0.5W | https://www.digikey.ca/en/products/detail/panasonic-electronic-components/ERJ-14NF1821U/383924
28 | 1 | R30 | 50k | Ebay – Kit
29 | 11 | R31, R52, R54, R55, R57, R58, R60, R61, R64, R65, R66 | 10k | https://www.digikey.ca/en/products/detail/stackpole-electronics-inc/RNCP0805FTD10K0/2240262
30 | 5 | R34, R53, R56, R62, R63 | 2.2k | Ebay – Kit
31 | 1 | R35 | 47k | Ebay – Kit
32 | 1 | R37 | 100k | Ebay – Kit
33 | 6 | R41, R43, R45, R47, R49, R51 | 5.62k | Ebay – Kit
34 | 1 | R59 | 1.5k | Ebay – Kit
35 | 1 | RV1 | B72510T0040M062 | https://www.digikey.ca/en/products/detail/epcos-tdk-electronics/B72510T0040M062/1091373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
36 | 7 | RV2, RV4, RV5, RV6, RV7, RV8, RV9 | VC080503A100DP | https://www.digikey.ca/en/products/detail/avx-corporation/VC080503A100DP/684850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
37 | 1 | RV3 | POT_10k | https://www.digikey.ca/en/products/detail/bourns-inc/PV36W103C01B00/666502
38 | 2 | SW1, SW2 | SW_Push | https://www.digikey.ca/en/products/detail/omron-electronics-inc-emc-div/B3F-1020/44059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
39 | 1 | U1 | NUP2114UCMR6T1G | https://www.digikey.ca/en/products/detail/on-semiconductor/NUP2114UCMR6T1G/1961288
40 | 7 | U2, U3, U4, U5, U6, U7, U8 | MOCD217R2M | https://www.digikey.ca/en/products/detail/on-semiconductor/MOCD217R2M/402226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
41 | 1 | U9 | TS912 | https://www.digikey.ca/en/products/detail/stmicroelectronics/TS912BIDT/1040337
42 | 1 | U10 | AP7381_SOT89 | https://www.digikey.ca/en/products/detail/diodes-incorporated/AP7381-33Y-13/7914854
43 | 1 | U11 | LM2937IMP-3.3 | https://www.digikey.ca/en/products/detail/texas-instruments/LM2937IMP-3-3/3701483
44 | 1 | U14 | LPC1769FBD100 | https://www.digikey.ca/en/products/detail/nxp-usa-inc/LPC1769FBD100K/13540940
45 | 1 | Y1 | 12MHz | https://www.digikey.ca/en/products/detail/abracon-llc/ABM3-12-000MHZ-D2Y-T/2344574

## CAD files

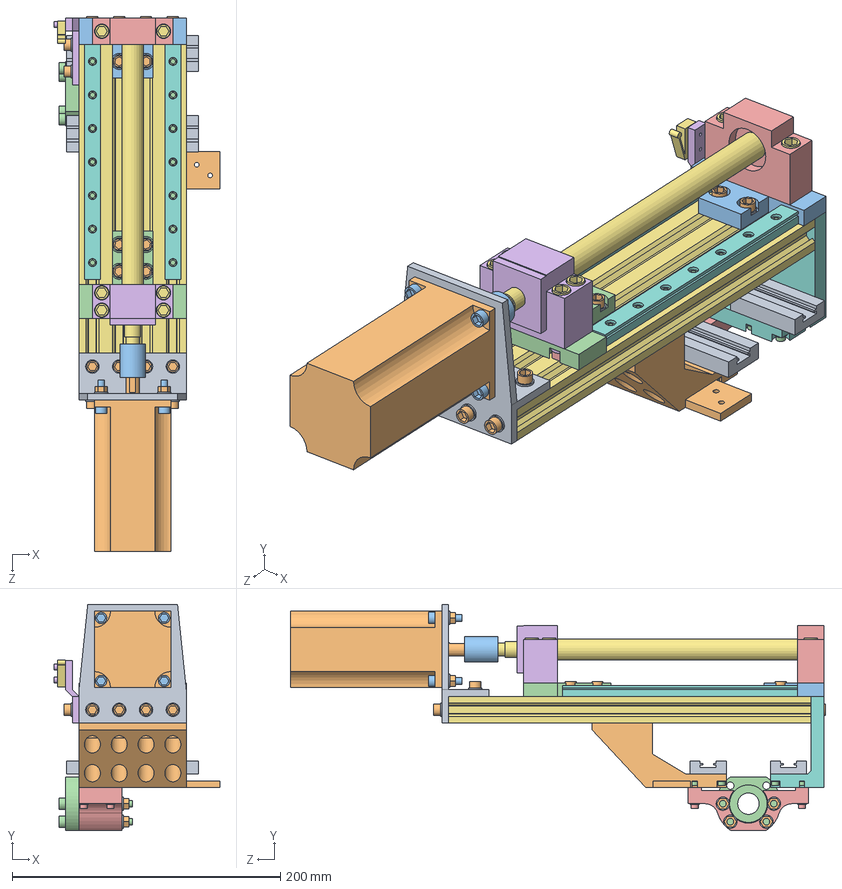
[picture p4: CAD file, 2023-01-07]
CAD/assemblies/Z frame.SLDASM
123.5 x 168.5 x 399.1 mm
M5 washer x 36
M5x10mm x 28
M3 washer x 16
M3x8mm x 26
M6 nut x 6
M6 washer x 6
M6x35mm x 6
M5 T nut x 20
M3 T nut x 14
M5 nut x 8
M5x20mm x 4
M5x50mm x 4
M3x25mm x 4
M2.5x10mm x 2
2080x270mm
Z frame support bottom
MGN12H x 4
Z frame support top
YZ frame BF12 spacer
YZ frame BK12 spacer
BF12
BK12
SFU1605x250mm
MGN12x175mm x 2
XZ frame motor support
Nema 23 3 Nm
coupler
SFU1605 nut
Y frame screw support
Z limit switch support
limit switch

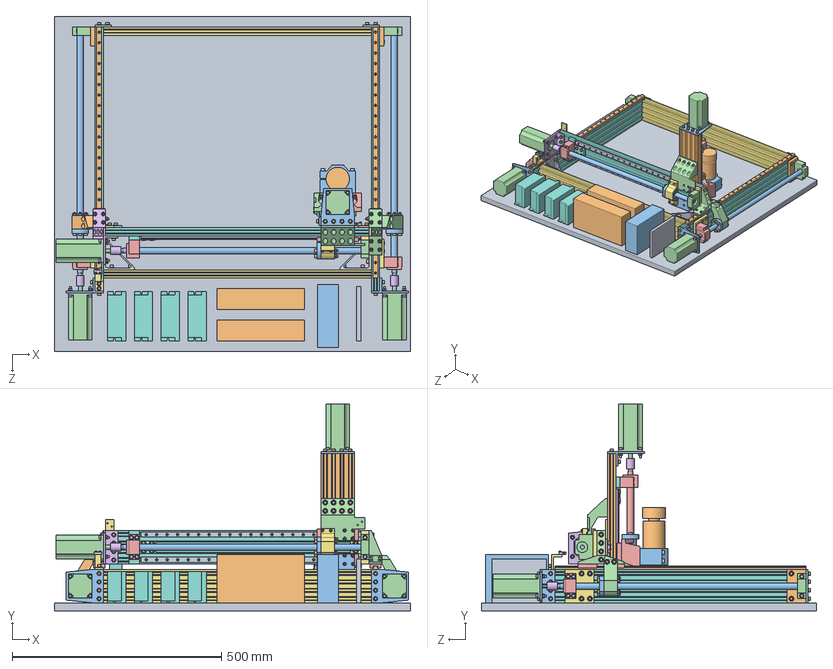
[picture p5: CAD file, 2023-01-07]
CAD/assemblies/table+CNC.SLDASM
850.0 x 493.5 x 800.0 mm
table
M5x10mm x 114
M5 washer x 156
M5 T nut x 82
M3x8mm x 140
M3 T nut x 104
2080x640mm x 2
2080x630mm x 3
X frame corner x 2
MGN12x600mm x 2
SFU1605x600mm x 3
BF12 x 4
BK12 x 4
coupler x 4
M6 nut x 28
M6 washer x 28
M6x35mm x 24
X frame BF12 spacer x 2
XZ frame motor support x 3
Nema 23 3 Nm x 4
M5 nut x 38
M5x20mm x 16
X frame BK12 spacer x 2
X frame corner plate x 2
M3 washer x 40
M5x50mm x 20
M2.5x10mm x 6
Y frame support right
MGN12H x 10
Y frame support left
YZ frame BF12 spacer x 2
YZ frame BK12 spacer x 2
MGN12x525mm x 2
X frame screw support left
SFU1605 nut x 4
X frame screw support right
Y limit switch support
limit switch x 3
Y cable tray support
X cable tray support
M3x25mm x 4
2080x270mm
Z frame support bottom
Z frame support top
SFU1605x250mm
MGN12x175mm x 2
Y frame screw support
Z limit switch support
M6x70mm x 4
spindle
spindle mount
spindle frame right
spindle frame left
M5x30mm x 2
X limit switch support
DM542 x 4
smoothieboard
PSU 24V x 2
PSU 100V

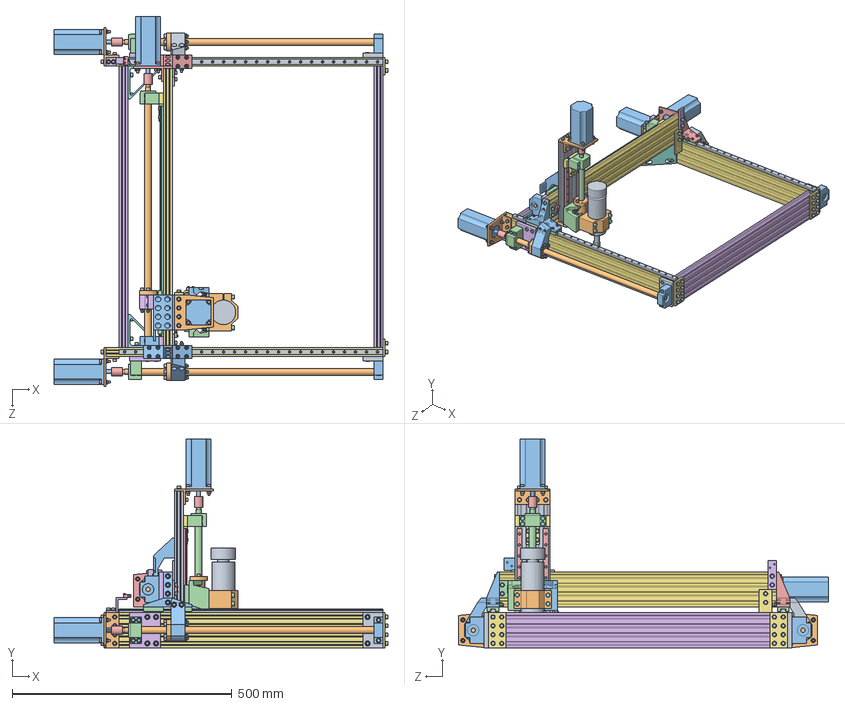
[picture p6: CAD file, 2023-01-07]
CAD/assemblies/CNC.SLDASM
759.1 x 474.5 x 841.5 mm
M5x10mm x 114
M5 washer x 156
M5 T nut x 82
M3x8mm x 140
M3 T nut x 104
2080x640mm x 2
2080x630mm x 3
X frame corner x 2
MGN12x600mm x 2
SFU1605x600mm x 3
BF12 x 4
BK12 x 4
coupler x 4
M6 nut x 28
M6 washer x 28
M6x35mm x 24
X frame BF12 spacer x 2
XZ frame motor support x 3
Nema 23 3 Nm x 4
M5 nut x 38
M5x20mm x 16
X frame BK12 spacer x 2
X frame corner plate x 2
M3 washer x 40
M5x50mm x 20
M2.5x10mm x 6
Y frame support right
MGN12H x 10
Y frame support left
YZ frame BF12 spacer x 2
YZ frame BK12 spacer x 2
MGN12x525mm x 2
X frame screw support left
SFU1605 nut x 4
X frame screw support right
Y limit switch support
limit switch x 3
Y cable tray support
X cable tray support
M3x25mm x 4
2080x270mm
Z frame support bottom
Z frame support top
SFU1605x250mm
MGN12x175mm x 2
Y frame screw support
Z limit switch support
M6x70mm x 4
spindle
spindle mount
spindle frame right
spindle frame left
M5x30mm x 2
X limit switch support

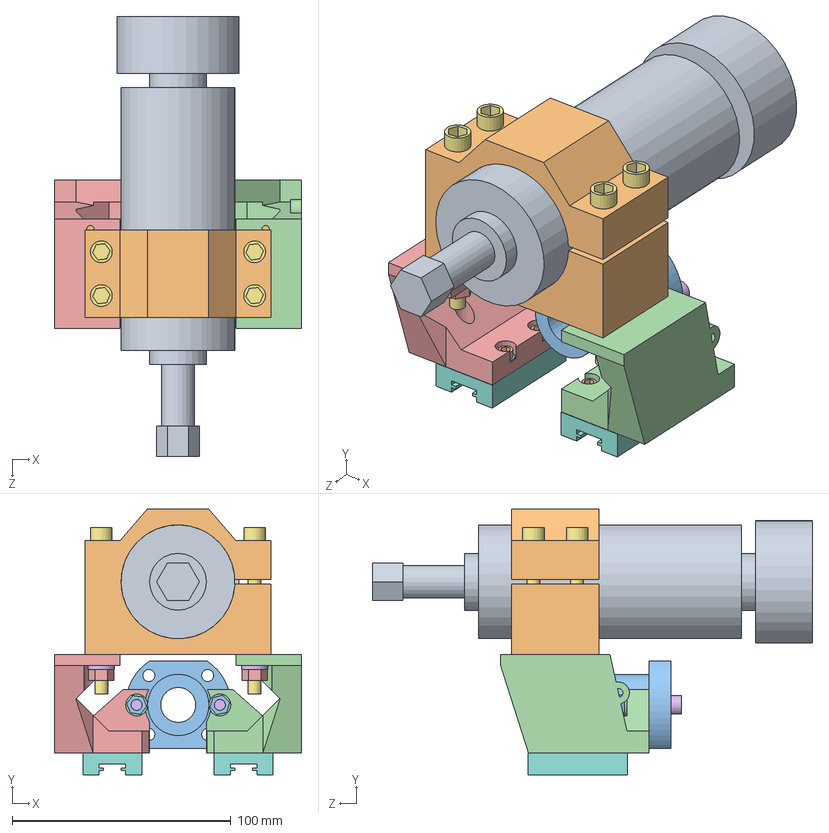
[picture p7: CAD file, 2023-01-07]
CAD/assemblies/spindle frame.SLDASM
113.0 x 121.5 x 201.0 mm
M3 washer x 8
M3x8mm x 8
M5 nut x 2
M5 washer x 2
M6 nut x 4
M6 washer x 4
M6x70mm x 4
MGN12H x 2
spindle
spindle mount
SFU1605 nut
spindle frame right
spindle frame left
M5x30mm x 2

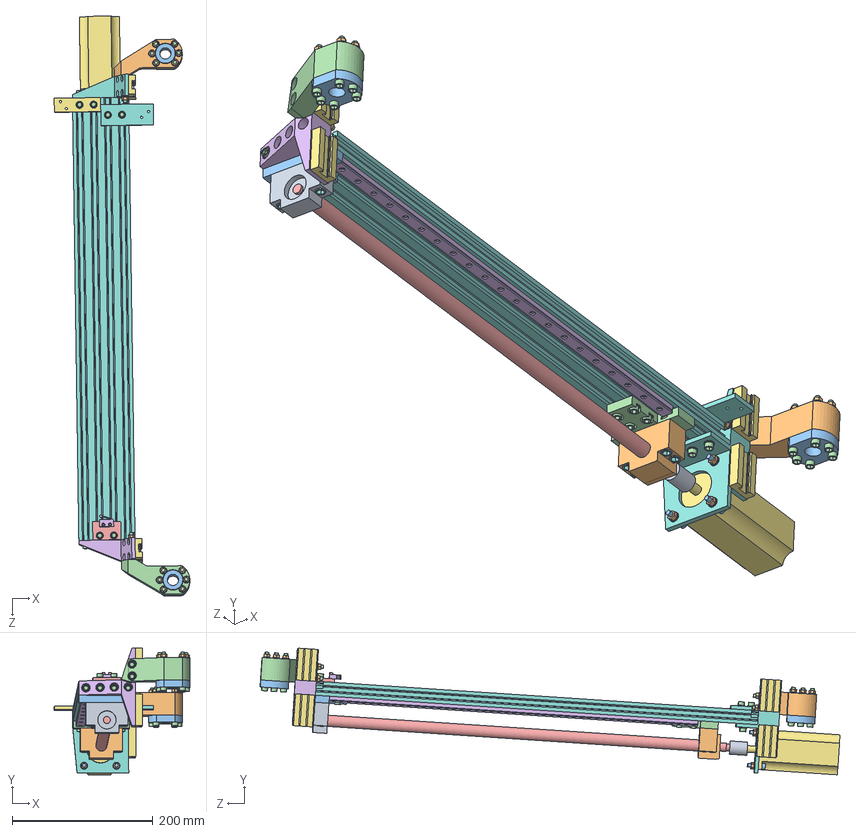
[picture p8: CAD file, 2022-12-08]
CAD/assemblies/Y frame.SLDASM
192.9 x 180.0 x 824.3 mm
M3 T nut x 42
M3x8mm x 58
M5 washer x 48
M5x10mm x 24
M3 washer x 16
M6 nut x 6
M6 washer x 6
M6x35mm x 6
M5 T nut x 16
M5 nut x 20
M5x20mm x 4
M5x50mm x 16
M2.5x10mm x 2
Y frame support right
MGN12H x 4
Y frame support left
BF12
BK12
YZ frame BF12 spacer
YZ frame BK12 spacer
SFU1605x600mm
MGN12x525mm x 2
Nema 23 3 Nm
2080x630mm
coupler
X frame screw support left
SFU1605 nut x 2
X frame screw support right
Y limit switch support
limit switch
Y cable tray support
X cable tray support

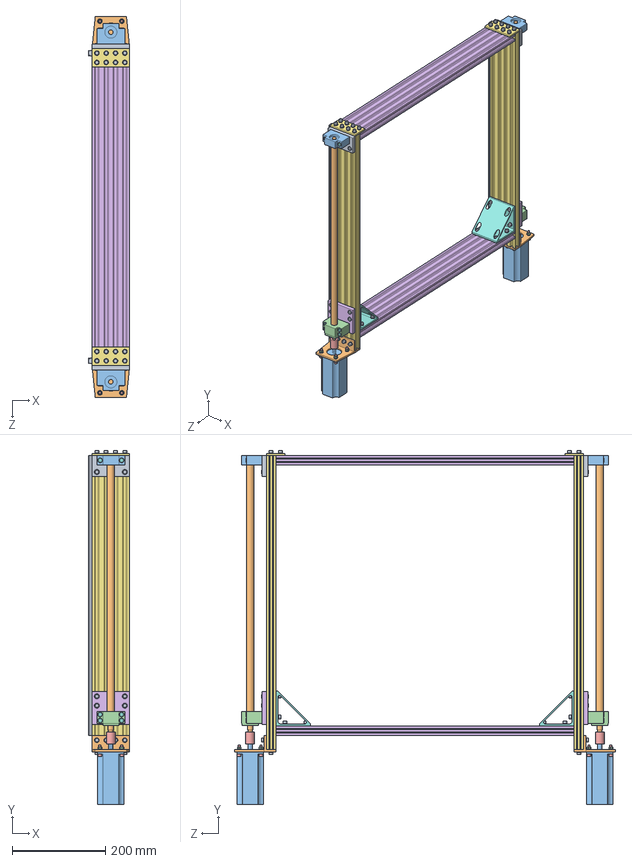
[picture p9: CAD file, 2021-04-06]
CAD/assemblies/X frame.SLDASM
88.0 x 759.1 x 817.0 mm
M5x10mm x 60
M5 washer x 68
M5 T nut x 44
M3x8mm x 48
M3 T nut x 48
2080x640mm x 2
2080x630mm x 2
X frame corner x 2
MGN12x600mm x 2
SFU1605x600mm x 2
BF12 x 2
BK12 x 2
coupler x 2
M6 nut x 12
M6 washer x 12
M6x35mm x 12
X frame BF12 spacer x 2
XZ frame motor support x 2
Nema 23 3 Nm x 2
M5 nut x 8
M5x20mm x 8
X frame BK12 spacer x 2
X frame corner plate x 2

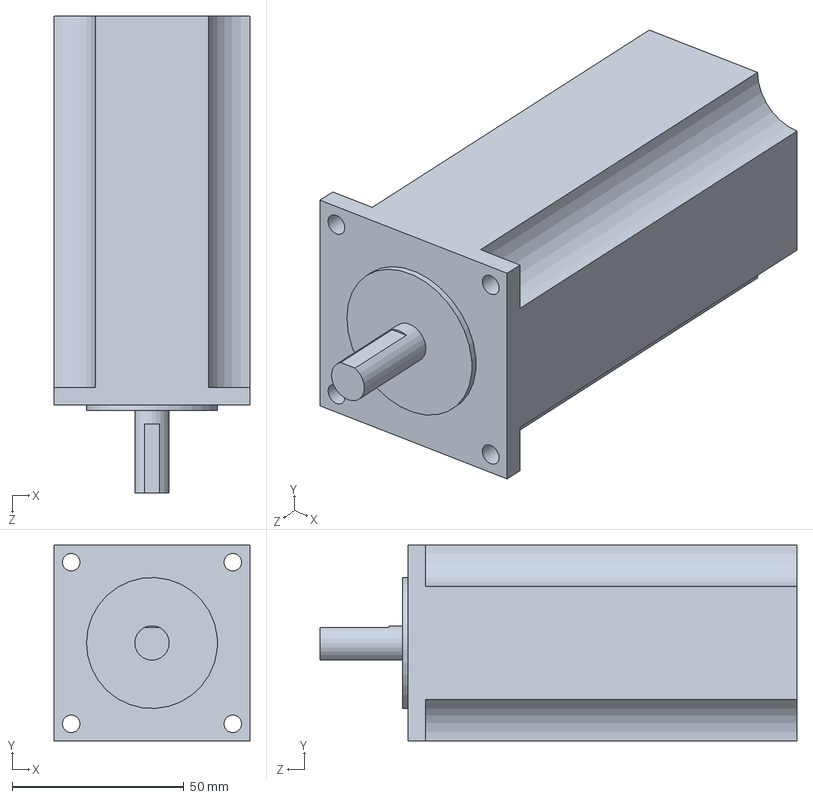
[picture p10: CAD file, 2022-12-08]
CAD/electronics/Nema 23 3 Nm.SLDPRT
57.0 x 57.0 x 138.6 mm

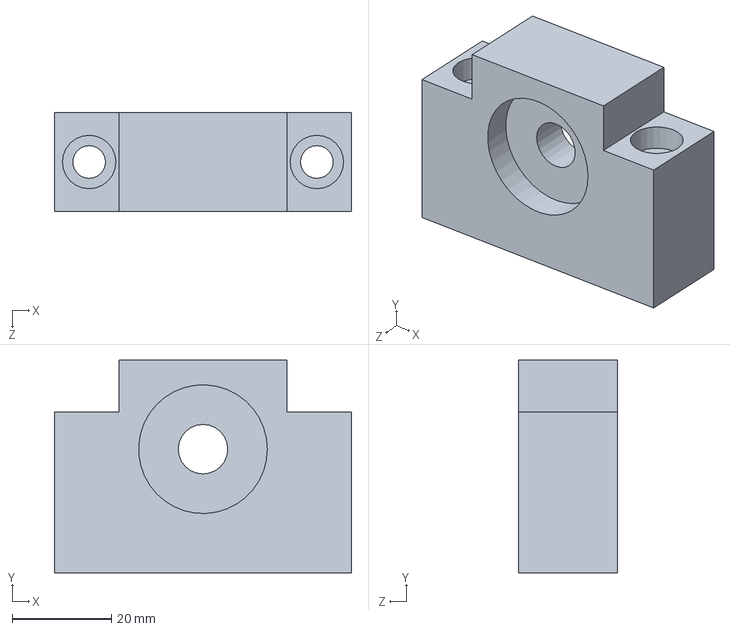
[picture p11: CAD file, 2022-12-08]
CAD/linear motion/BF12.SLDPRT
60.0 x 43.0 x 20.0 mm

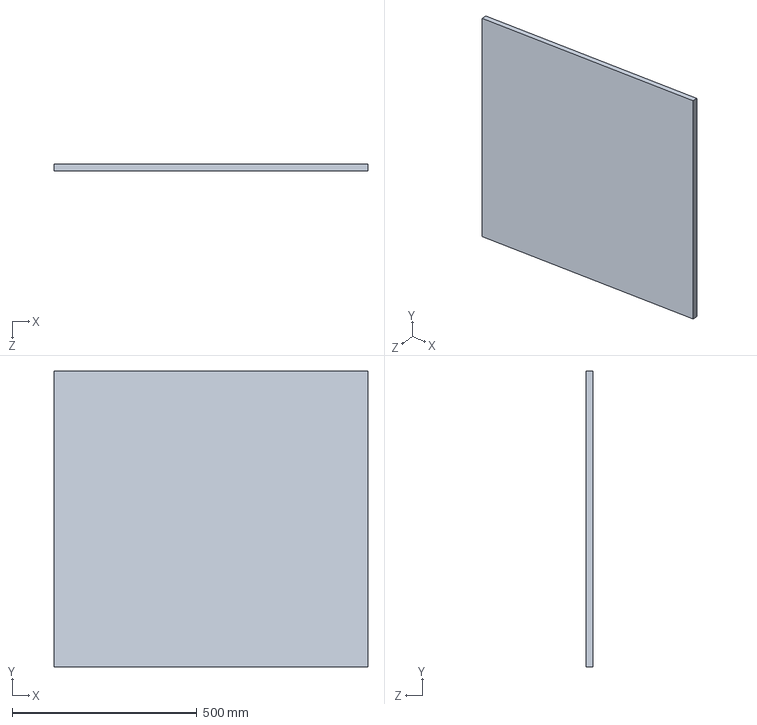
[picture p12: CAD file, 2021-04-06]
CAD/table/table.SLDPRT
850.0 x 800.0 x 19.1 mm

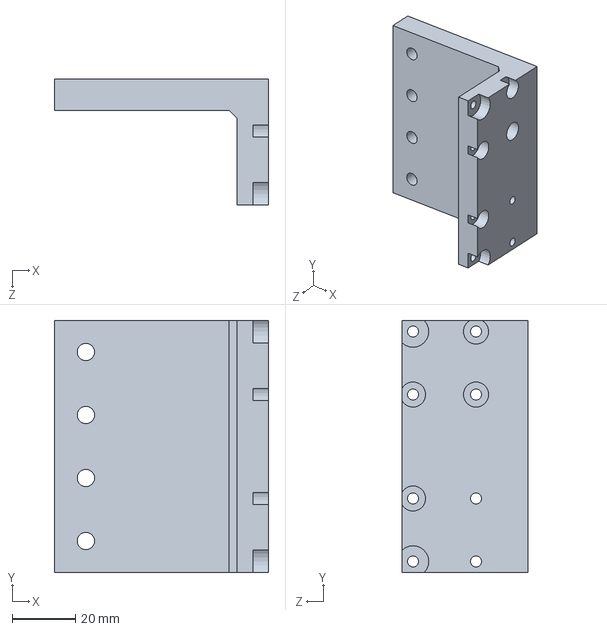
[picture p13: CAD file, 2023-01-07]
CAD/3d printed parts/Z frame support bottom.SLDPRT
68.0 x 80.0 x 40.0 mm

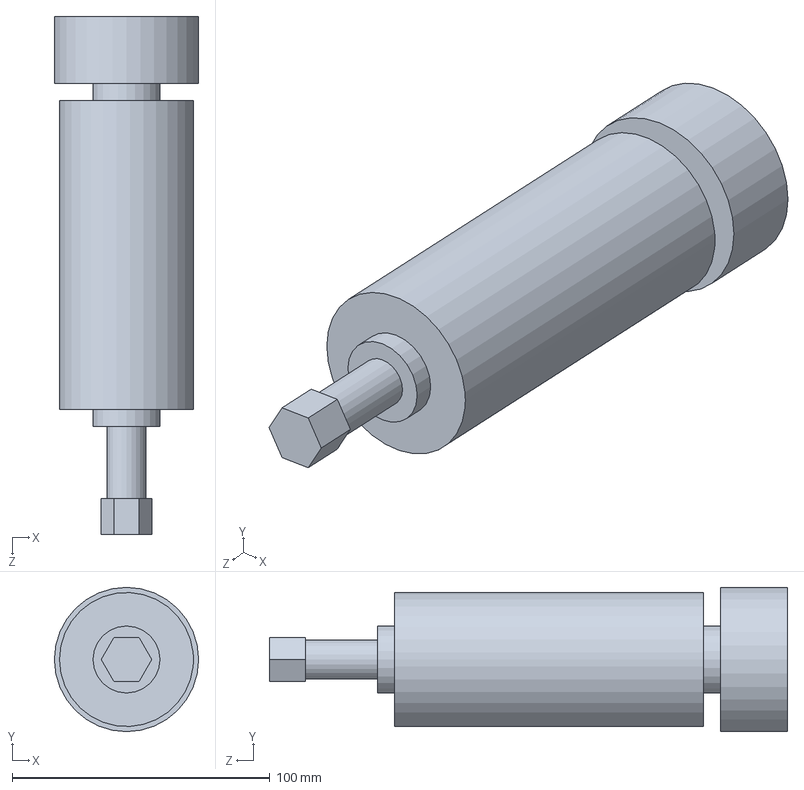
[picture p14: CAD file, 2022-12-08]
CAD/electronics/spindle.SLDPRT
56.0 x 56.0 x 201.0 mm

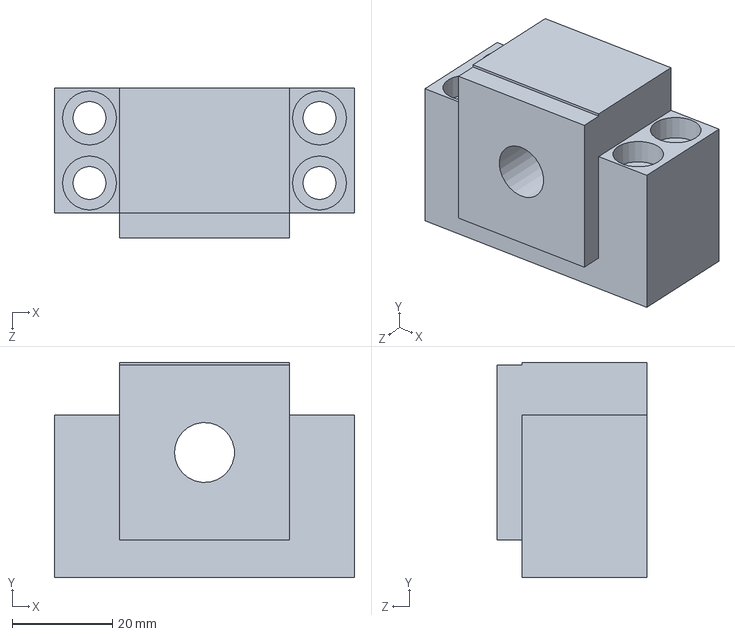
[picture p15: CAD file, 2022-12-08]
CAD/linear motion/BK12.SLDPRT
60.0 x 43.0 x 30.0 mm

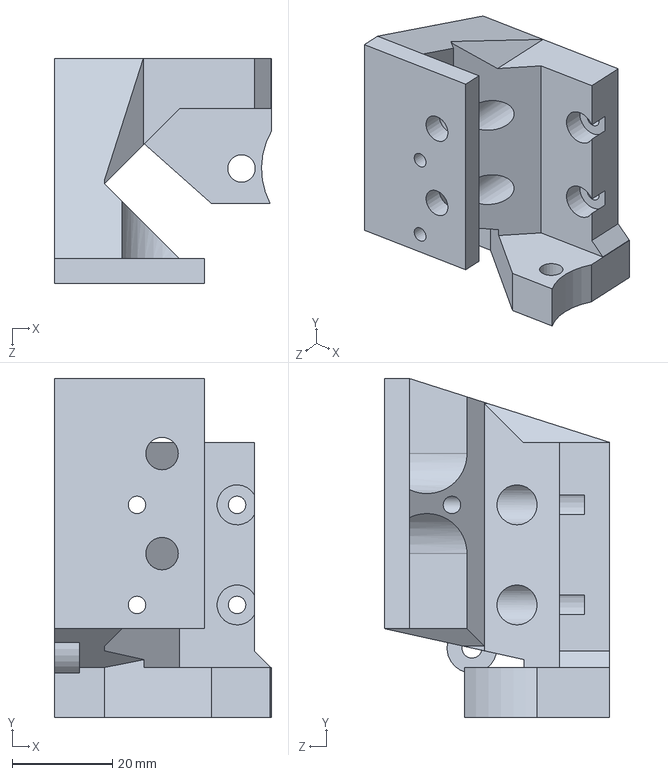
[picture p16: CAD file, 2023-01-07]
CAD/3d printed parts/spindle frame right.SLDPRT
43.4 x 67.8 x 45.0 mm

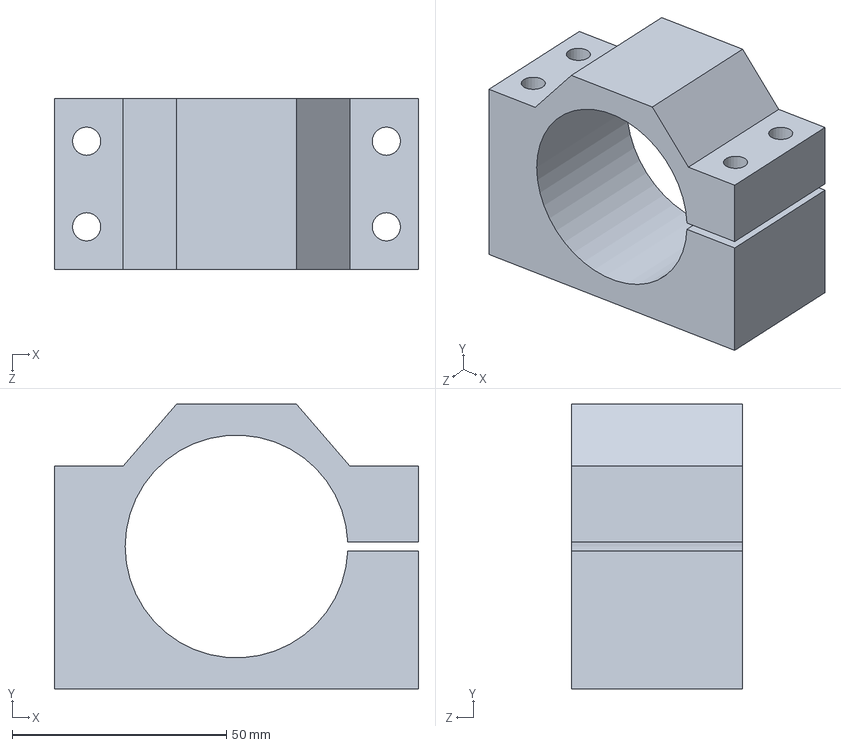
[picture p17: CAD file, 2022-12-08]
CAD/electronics/spindle mount.SLDPRT
85.0 x 66.5 x 40.0 mm

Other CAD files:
CAD/linear motion/MGN12x525mm.SLDPRT
CAD/3d printed parts/Z limit switch support.SLDPRT
CAD/electronics/limit switch.SLDPRT
CAD/linear motion/coupler.SLDPRT
CAD/3d printed parts/X cable tray support.SLDPRT
CAD/3d printed parts/X frame BF12 spacer.SLDPRT
CAD/3d printed parts/X frame BK12 spacer.SLDPRT
CAD/3d printed parts/X frame corner plate.SLDPRT
CAD/3d printed parts/X frame corner.SLDPRT
CAD/3d printed parts/X frame screw support left.SLDPRT
CAD/3d printed parts/X frame screw support right.SLDPRT
CAD/3d printed parts/X limit switch support.SLDPRT
CAD/3d printed parts/XZ frame motor support.SLDPRT
CAD/3d printed parts/Y cable tray support.SLDPRT
CAD/3d printed parts/Y frame screw support.SLDPRT
CAD/3d printed parts/Y frame support left.SLDPRT
CAD/3d printed parts/Y frame support right.SLDPRT
CAD/3d printed parts/Y limit switch support.SLDPRT
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

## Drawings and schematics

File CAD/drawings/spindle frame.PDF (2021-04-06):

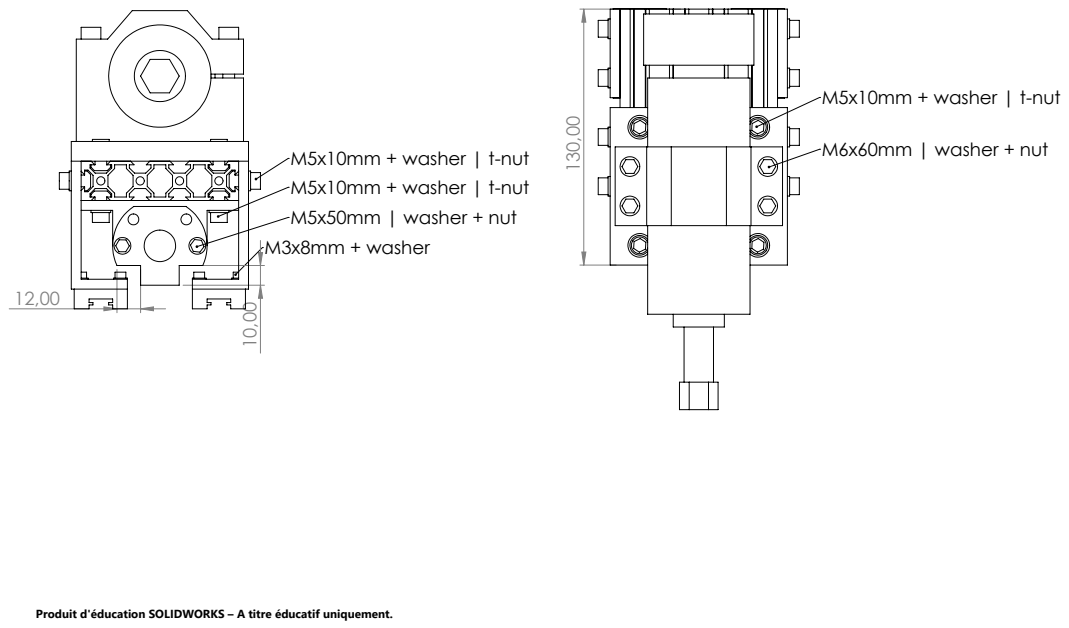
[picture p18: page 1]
M3x8mm + washer; M5x10mm + washer | t-nut M5x10mm + washer | t-nut M5x50mm | washer + nut; M5x10mm + washer | t-nut; M6x60mm | washer + nut

Produit d'éducation SOLIDWORKS – A titre éducatif uniquement.

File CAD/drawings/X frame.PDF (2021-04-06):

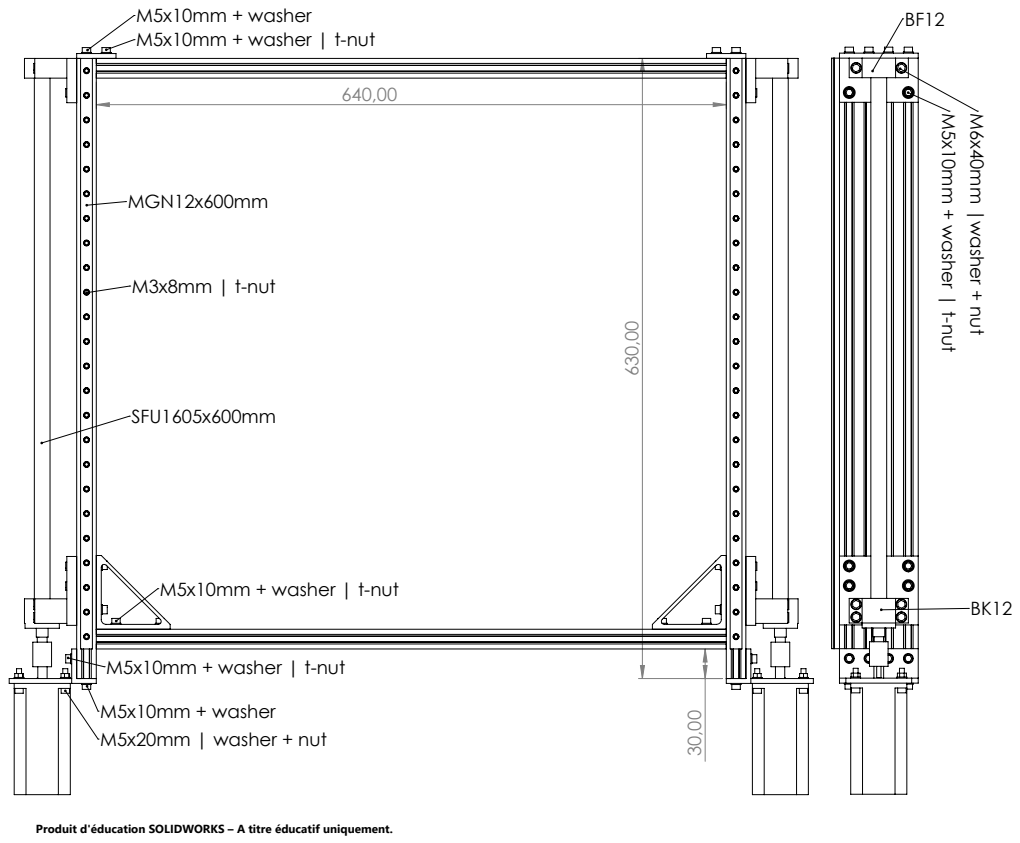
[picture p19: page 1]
M3x8mm | t-nut; M5x10mm + washer | t-nut; M5x10mm + washer; M5x20mm | washer + nut; M6x40mm |washer + nut

Produit d'éducation SOLIDWORKS – A titre éducatif uniquement.

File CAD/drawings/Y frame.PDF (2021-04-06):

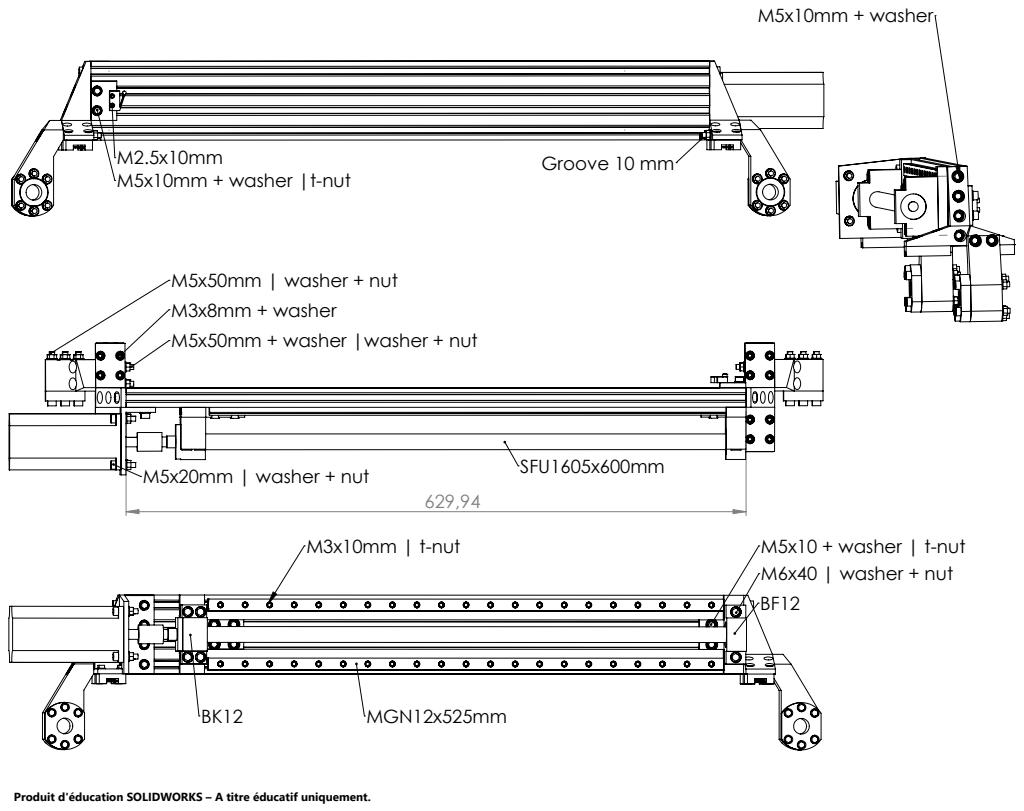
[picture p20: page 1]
M3x10mm | t-nut; M6x40 | washer + nut; M5x10 + washer | t-nut; M5x20mm | washer + nut; SFU1605x600mm; M5x10mm + washer |t-nut; Groove 10 mm; M5x10mm + washer

M5x50mm | washer + nut
M3x8mm + washer
M5x50mm + washer |washer + nut

Produit d'éducation SOLIDWORKS – A titre éducatif uniquement.

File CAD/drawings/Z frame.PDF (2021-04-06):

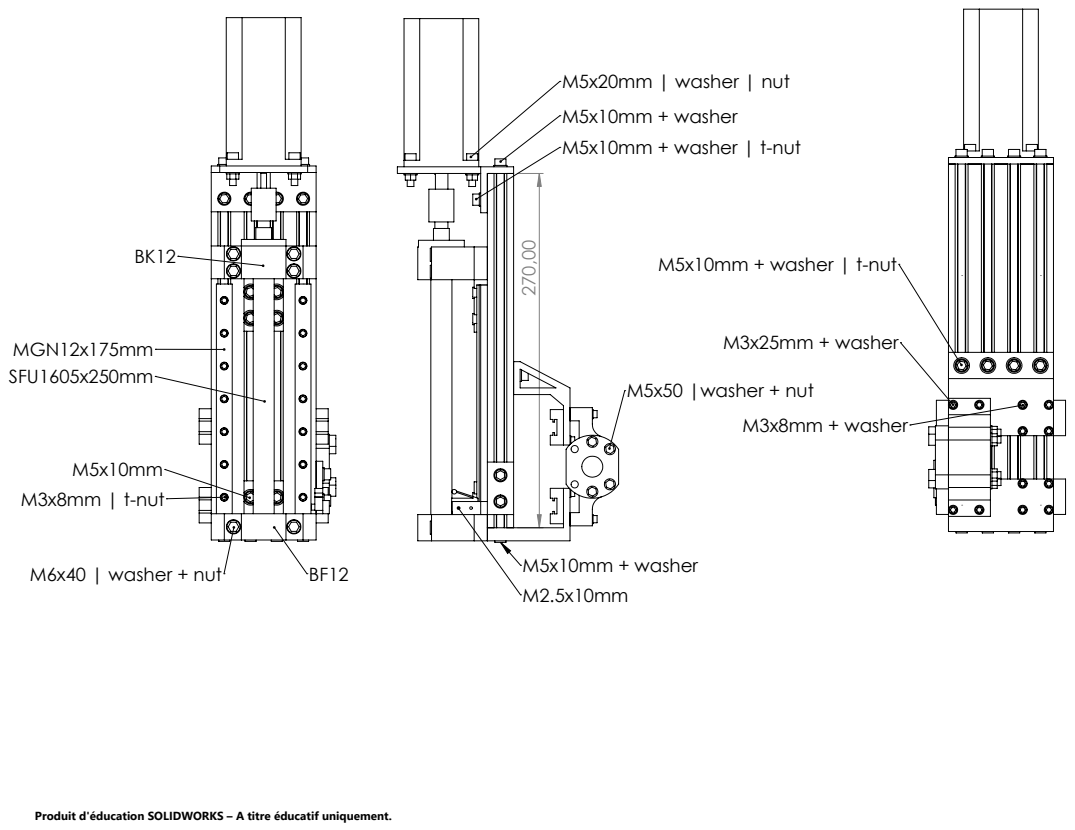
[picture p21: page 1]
M5x10mm + washer M5x10mm + washer | t-nut; M5x20mm | washer | nut; M5x50 |washer + nut; M5x10mm + washer; M3x8mm + washer; M3x25mm + washer; M5x10mm + washer | t-nut; M3x8mm | t-nut; M6x40 | washer + nut

Produit d'éducation SOLIDWORKS – A titre éducatif uniquement.

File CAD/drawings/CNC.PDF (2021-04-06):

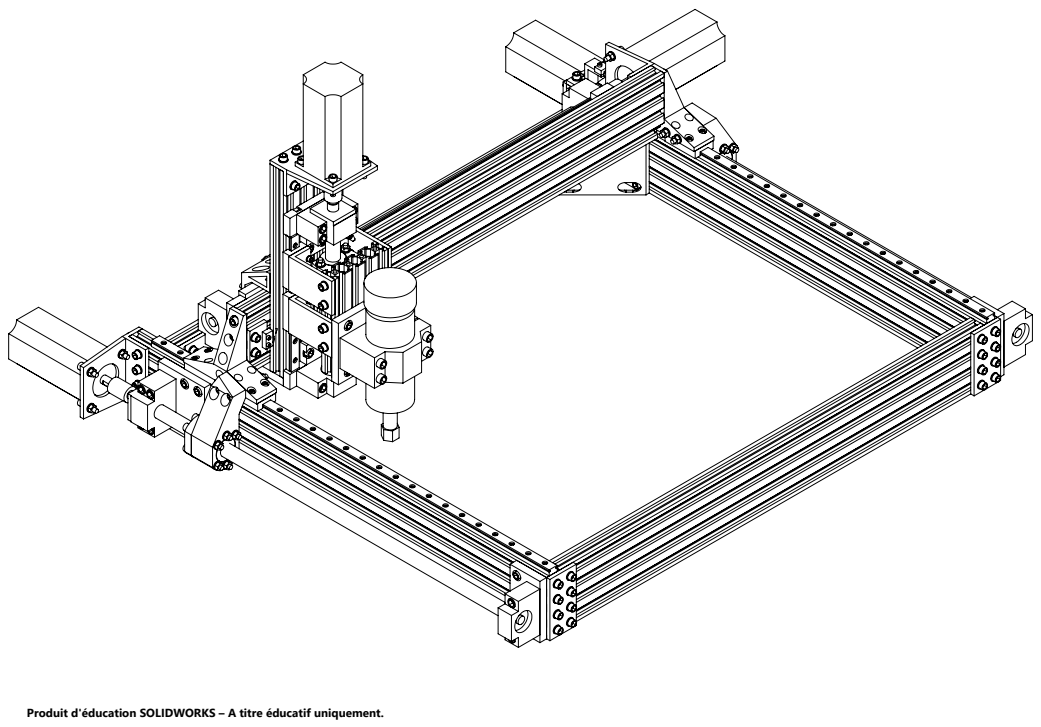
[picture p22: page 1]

Produit d'éducation SOLIDWORKS – A titre éducatif uniquement.

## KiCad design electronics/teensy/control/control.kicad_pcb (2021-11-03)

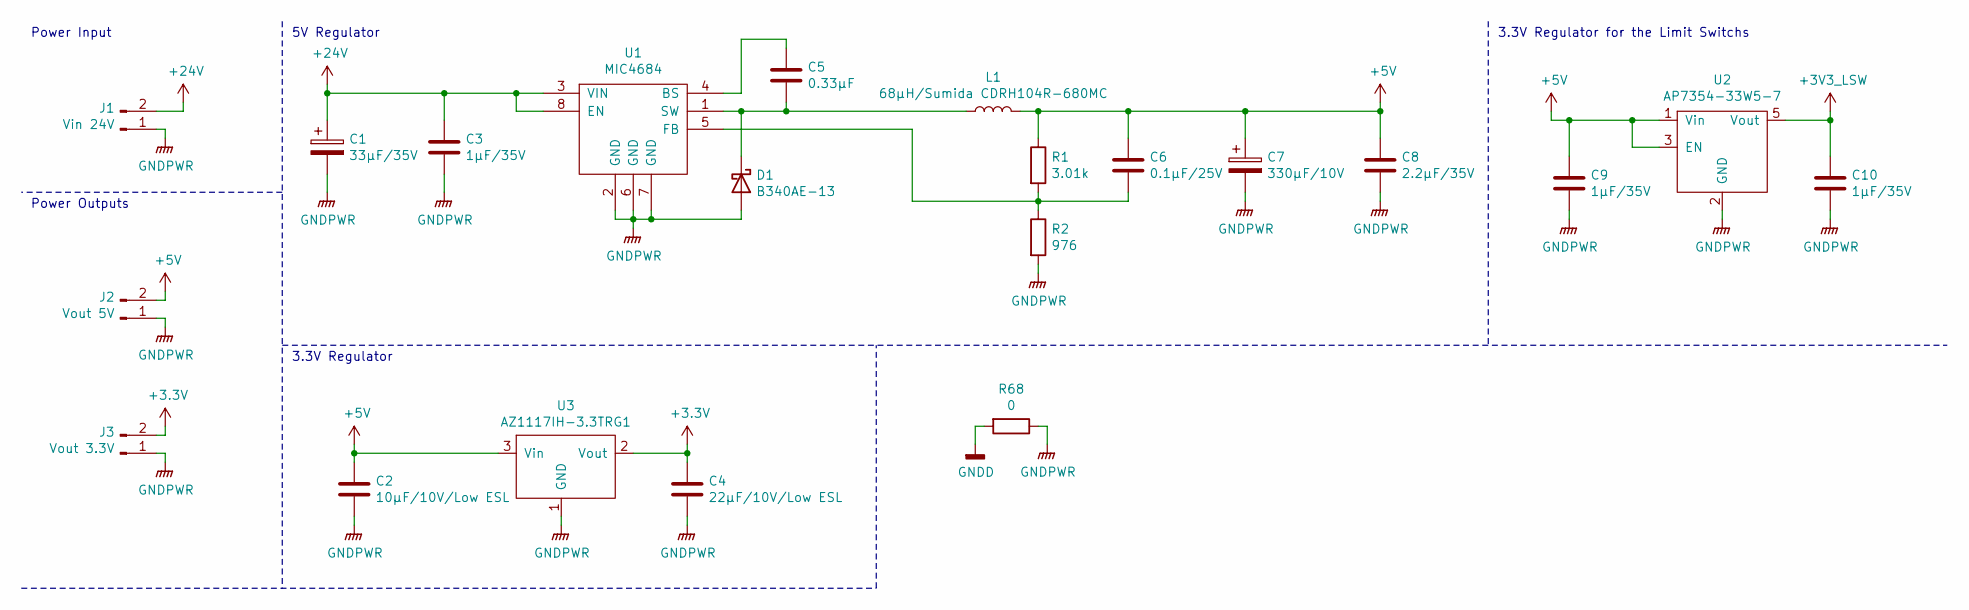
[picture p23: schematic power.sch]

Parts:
C1: 33µF/35V; CP_Radial_D10.0mm_P5.00mm
C2: 10µF/10V/Low ESL; C_0805_2012Metric
C3, C9, C10: 1µF/35V; C_0805_2012Metric
C4: 22µF/10V/Low ESL; C_0805_2012Metric
C5: 0.33µF; C_0805_2012Metric
C6: 0.1µF/25V; C_0805_2012Metric
C7: 330µF/10V; CP_Radial_D10.0mm_P5.00mm
C8: 2.2µF/35V; C_0805_2012Metric
D1: B340AE-13; D_SMB
J1: Vin 24V; EBWA-02-B
J2: Vout 5V; JST_XH_B2B-XH-A_1x02_P2.50mm_Vertical
J3: Vout 3.3V; JST_XH_B2B-XH-A_1x02_P2.50mm_Vertical
L1: 68µH/Sumida CDRH104R-680MC; CDRH104RNP-680NC
R1: 3.01k; R_0805_2012Metric
R2: 976; R_0805_2012Metric
R68: 0; R_1206_3216Metric
U1: MIC4684; SOIC-8_3.9x4.9mm_P1.27mm
U2: AP7354-33W5-7; SOT-23-5
U3: AZ1117IH-3.3TRG1; SOT-223-3_TabPin2

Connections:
+3V3: C4.1, J3.2, U3.2 (Vout); also elsewhere on the board
+3V3_LSW: C10.1, U2.5 (Vout); also elsewhere on the board
+5V: C2.1, C6.1, C7.1, C8.1, C9.1, J2.2, L1.2, R1.1, U2.1 (Vin), U2.3 (EN), U3.3 (Vin); also elsewhere on the board
+24V: C1.1, C3.1, J1.2, U1.3 (VIN), U1.8 (EN)
GNDD: R68.2; also elsewhere on the board
GNDPWR: C1.2, C2.2, C3.2, C4.2, C7.2, C8.2, C9.2, C10.2, D1.2 (A), J1.1, J2.1, J3.1, R2.2, R68.1, U1.2 (GND), U1.6 (GND), U1.7 (GND), U2.2 (GND), U3.1 (GND)
unnamed: C5.1, U1.4 (BS)
unnamed: C5.2, D1.1 (K), L1.1, U1.1 (SW)
unnamed: C6.2, R1.2, R2.1, U1.5 (FB)

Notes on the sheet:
Power Input
5V Regulator
3.3V Regulator for the Limit Switchs
3.3V Regulator
Power Outputs

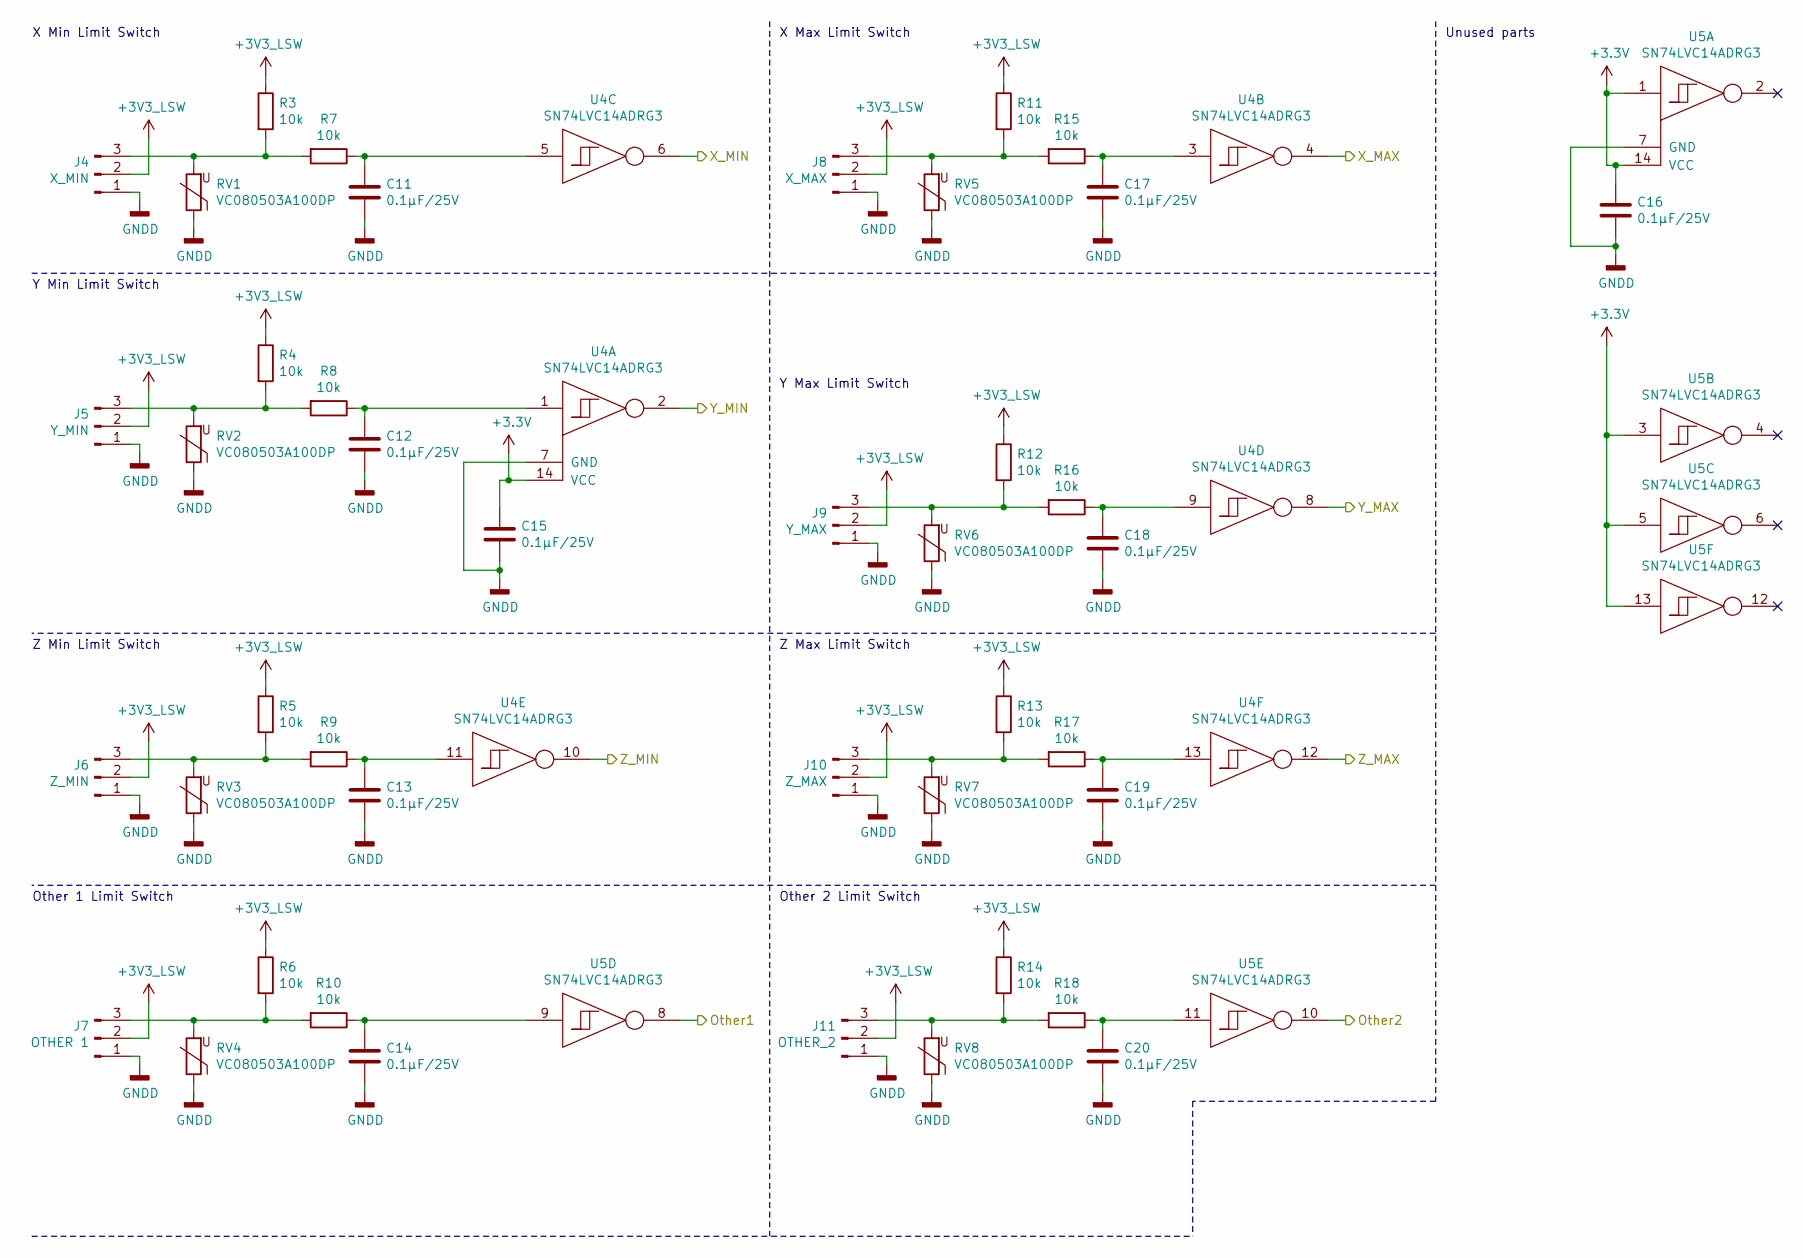
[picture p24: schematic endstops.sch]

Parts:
C11, C12, C13, C14, C15, C16, C17, C18, C19, C20: 0.1µF/25V; C_0805_2012Metric
J4: X_MIN; JST_XH_B3B-XH-A_1x03_P2.50mm_Vertical
J5: Y_MIN; JST_XH_B3B-XH-A_1x03_P2.50mm_Vertical
J6: Z_MIN; JST_XH_B3B-XH-A_1x03_P2.50mm_Vertical
J7: OTHER 1; JST_XH_B3B-XH-A_1x03_P2.50mm_Vertical
J8: X_MAX; JST_XH_B3B-XH-A_1x03_P2.50mm_Vertical
J9: Y_MAX; JST_XH_B3B-XH-A_1x03_P2.50mm_Vertical
J10: Z_MAX; JST_XH_B3B-XH-A_1x03_P2.50mm_Vertical
J11: OTHER_2; JST_XH_B3B-XH-A_1x03_P2.50mm_Vertical
R3, R4, R5, R6, R7, R8, R9, R10, R11, R12, R13, R14, R15, R16, R17, R18: 10k; R_0805_2012Metric
RV1, RV2, RV3, RV4, RV5, RV6, RV7, RV8: VC080503A100DP; R_0805_2012Metric
U4, U5: SN74LVC14ADRG3; SOIC-14_3.9x8.7mm_P1.27mm

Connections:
+3V3: C15.1, C16.1, U4.14 (VCC), U5.1, U5.3, U5.5, U5.13, U5.14 (VCC); also elsewhere on the board
+3V3_LSW: J4.2, J5.2, J6.2, J7.2, J8.2, J9.2, J10.2, J11.2, R3.1, R4.1, R5.1, R6.1, R11.1, R12.1, R13.1, R14.1; also elsewhere on the board
/endstops/X_MAX: U4.4; also elsewhere on the board
/endstops/X_MIN: U4.6; also elsewhere on the board
/endstops/Y_MAX: U4.8; also elsewhere on the board
/endstops/Y_MIN: U4.2; also elsewhere on the board
/endstops/Z_MAX: U4.12; also elsewhere on the board
/endstops/Z_MIN: U4.10; also elsewhere on the board
/mcu/OTHER_1_ENDSTOP: U5.8; also elsewhere on the board
/mcu/OTHER_2_ENDSTOP: U5.10; also elsewhere on the board
GNDD: C11.2, C12.2, C13.2, C14.2, C15.2, C16.2, C17.2, C18.2, C19.2, C20.2, J4.1, J5.1, J6.1, J7.1, J8.1, J9.1, J10.1, J11.1, RV1.1, RV2.1, RV3.1, RV4.1, RV5.1, RV6.1, RV7.1, RV8.1, U4.7 (GND), U5.7 (GND); also elsewhere on the board
unnamed: C11.1, R7.1, U4.5
unnamed: C12.1, R8.1, U4.1
unnamed: C13.1, R9.1, U4.11
unnamed: C14.1, R10.1, U5.9
unnamed: C17.1, R15.1, U4.3
unnamed: C18.1, R16.1, U4.9
unnamed: C19.1, R17.1, U4.13
unnamed: C20.1, R18.1, U5.11
unnamed: J4.3, R3.2, R7.2, RV1.2
unnamed: J5.3, R4.2, R8.2, RV2.2
unnamed: J6.3, R5.2, R9.2, RV3.2
unnamed: J7.3, R6.2, R10.2, RV4.2
unnamed: J8.3, R11.2, R15.2, RV5.2
unnamed: J9.3, R12.2, R16.2, RV6.2
unnamed: J10.3, R13.2, R17.2, RV7.2
unnamed: J11.3, R14.2, R18.2, RV8.2

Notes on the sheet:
X Min Limit Switch
Y Min Limit Switch
Z Min Limit Switch
Z Max Limit Switch
Y Max Limit Switch
X Max Limit Switch
Other 2 Limit Switch
Other 1 Limit Switch
Unused parts

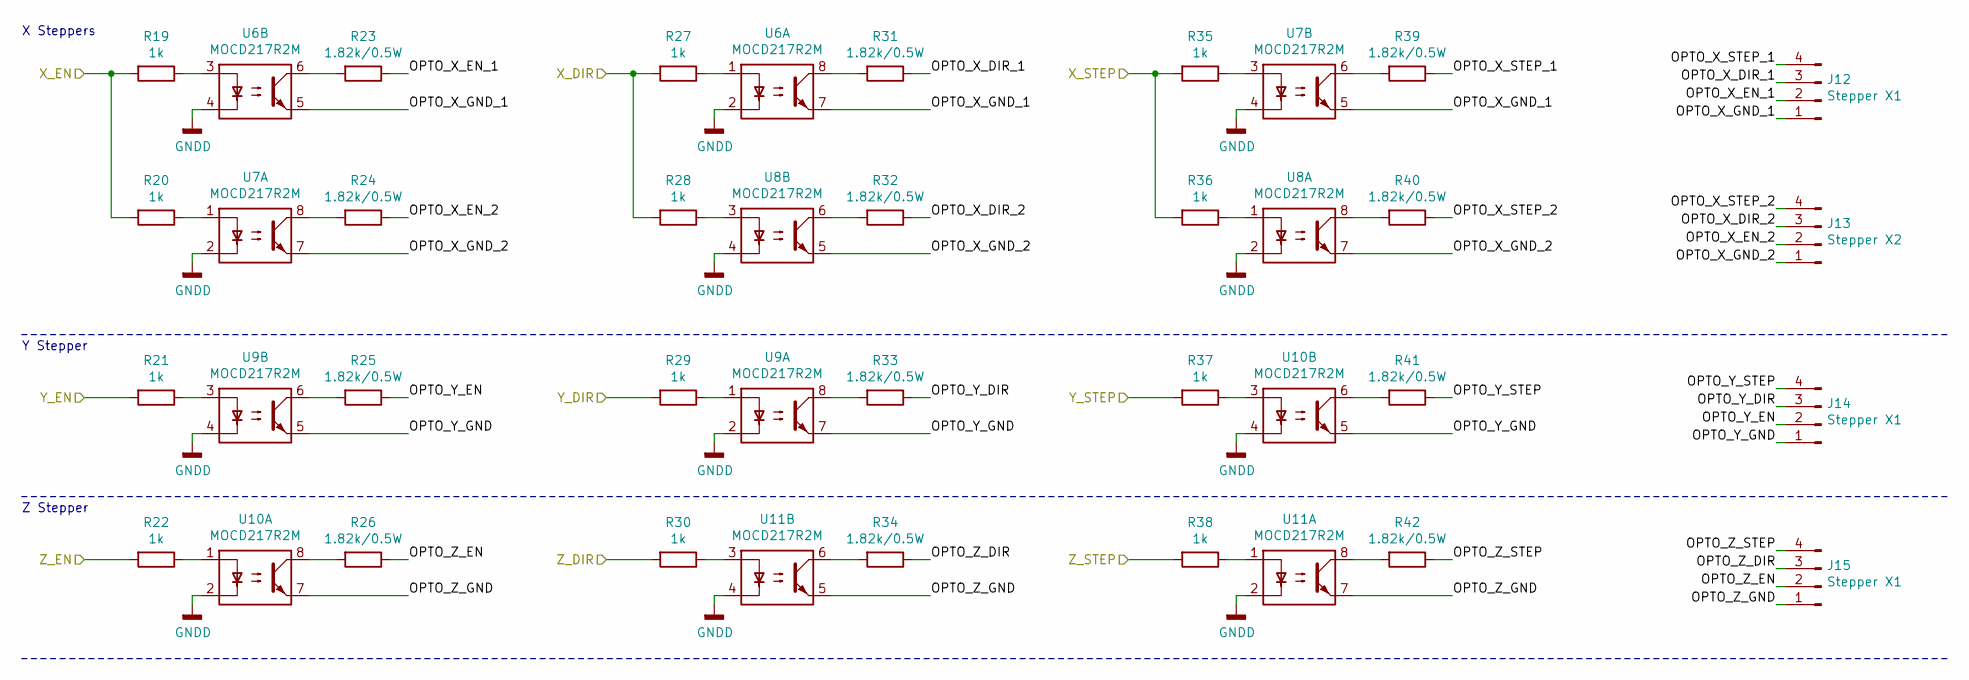
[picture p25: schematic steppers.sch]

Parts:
J12, J14, J15: Stepper X1; JST_XH_B4B-XH-A_1x04_P2.50mm_Vertical
J13: Stepper X2; JST_XH_B4B-XH-A_1x04_P2.50mm_Vertical
R19, R20, R21, R22, R27, R28, R29, R30, R35, R36, R37, R38: 1k; R_0805_2012Metric
R23, R24, R25, R26, R31, R32, R33, R34, R39, R40, R41, R42: 1.82k/0.5W; R_1206_3216Metric
U6, U7, U8, U9, U10, U11: MOCD217R2M; SOIC-8_3.9x4.9mm_P1.27mm

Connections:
/steppers/OPTO_X_DIR_1: J12.3, R31.1
/steppers/OPTO_X_DIR_2: J13.3, R32.1
/steppers/OPTO_X_EN_1: J12.2, R23.1
/steppers/OPTO_X_EN_2: J13.2, R24.1
/steppers/OPTO_X_GND_1: J12.1, U6.5, U6.7, U7.5
/steppers/OPTO_X_GND_2: J13.1, U7.7, U8.5, U8.7
/steppers/OPTO_X_STEP_1: J12.4, R39.1
/steppers/OPTO_X_STEP_2: J13.4, R40.1
/steppers/OPTO_Y_DIR: J14.3, R33.1
/steppers/OPTO_Y_EN: J14.2, R25.1
/steppers/OPTO_Y_GND: J14.1, U9.5, U9.7, U10.5
/steppers/OPTO_Y_STEP: J14.4, R41.1
/steppers/OPTO_Z_DIR: J15.3, R34.1
/steppers/OPTO_Z_EN: J15.2, R26.1
/steppers/OPTO_Z_GND: J15.1, U10.7, U11.5, U11.7
/steppers/OPTO_Z_STEP: J15.4, R42.1
/steppers/X_DIR: R27.2, R28.2; also elsewhere on the board
/steppers/X_EN: R19.2, R20.2; also elsewhere on the board
/steppers/X_STEP: R35.2, R36.2; also elsewhere on the board
/steppers/Y_DIR: R29.2; also elsewhere on the board
/steppers/Y_EN: R21.2; also elsewhere on the board
/steppers/Y_STEP: R37.2; also elsewhere on the board
/steppers/Z_DIR: R30.2; also elsewhere on the board
/steppers/Z_EN: R22.2; also elsewhere on the board
/steppers/Z_STEP: R38.2; also elsewhere on the board
GNDD: U6.2, U6.4, U7.2, U7.4, U8.2, U8.4, U9.2, U9.4, U10.2, U10.4, U11.2, U11.4; also elsewhere on the board
unnamed: R19.1, U6.3
unnamed: R20.1, U7.1
unnamed: R21.1, U9.3
unnamed: R22.1, U10.1
unnamed: R23.2, U6.6
unnamed: R24.2, U7.8
unnamed: R25.2, U9.6
unnamed: R26.2, U10.8
unnamed: R27.1, U6.1
unnamed: R28.1, U8.3
unnamed: R29.1, U9.1
unnamed: R30.1, U11.3
unnamed: R31.2, U6.8
unnamed: R32.2, U8.6
unnamed: R33.2, U9.8
unnamed: R34.2, U11.6
unnamed: R35.1, U7.3
unnamed: R36.1, U8.1
unnamed: R37.1, U10.3
unnamed: R38.1, U11.1
unnamed: R39.2, U7.6
unnamed: R40.2, U8.8
unnamed: R41.2, U10.6
unnamed: R42.2, U11.8

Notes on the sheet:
X Steppers
Y Stepper
Z Stepper

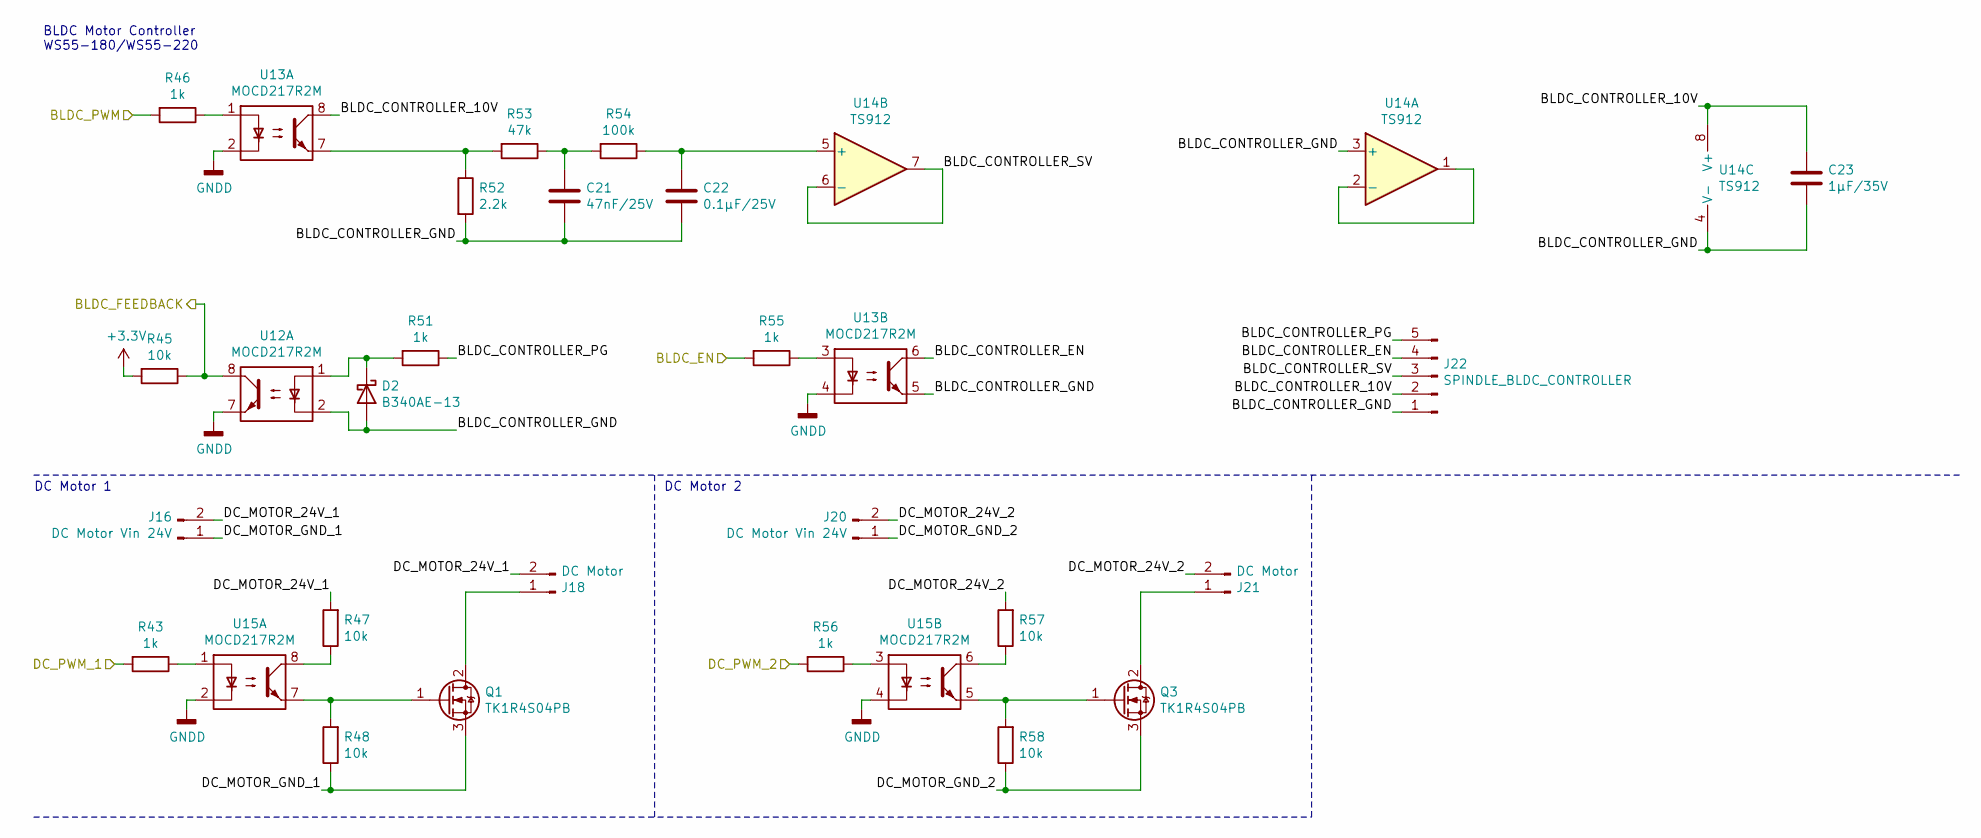
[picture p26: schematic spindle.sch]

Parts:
C21: 47nF/25V; C_0805_2012Metric
C22: 0.1µF/25V; C_0805_2012Metric
C23: 1µF/35V; C_0805_2012Metric
D2: B340AE-13; D_SMB
J16, J20: DC Motor Vin 24V; EBWA-02-B
J18, J21: DC Motor; EBWA-02-B
J22: SPINDLE_BLDC_CONTROLLER; JST_XH_B5B-XH-A_1x05_P2.50mm_Vertical
Q1, Q3: TK1R4S04PB; TO-252-2
R43, R46, R51, R55, R56: 1k; R_0805_2012Metric
R45, R47, R48, R57, R58: 10k; R_0805_2012Metric
R52: 2.2k; R_0805_2012Metric
R53: 47k; R_0805_2012Metric
R54: 100k; R_0805_2012Metric
U12, U13, U15: MOCD217R2M; SOIC-8_3.9x4.9mm_P1.27mm
U14: TS912; SOIC-8_3.9x4.9mm_P1.27mm

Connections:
+3V3: R45.2; also elsewhere on the board
/mcu/BLDC_MOTOR_PWM: R46.2; also elsewhere on the board
/mcu/DC_MOTOR_PWM_1: R43.2; also elsewhere on the board
/mcu/DC_MOTOR_PWM_2: R56.2; also elsewhere on the board
/spindle/BLDC_CONTROLLER_10V: C23.1, J22.2, U13.8, U14.8 (V+)
/spindle/BLDC_CONTROLLER_EN: J22.4, U13.6
/spindle/BLDC_CONTROLLER_GND: C21.2, C22.2, C23.2, D2.2 (A), J22.1, R52.2, U12.2, U13.5, U14.3 (+), U14.4 (V-)
/spindle/BLDC_CONTROLLER_PG: J22.5, R51.1
/spindle/BLDC_CONTROLLER_SV: J22.3, U14.6 (-), U14.7
/spindle/BLDC_EN: R55.2; also elsewhere on the board
/spindle/BLDC_FEEDBACK: R45.1, U12.8; also elsewhere on the board
/spindle/DC_MOTOR_24V_1: J16.2, J18.2, R47.2
/spindle/DC_MOTOR_24V_2: J20.2, J21.2, R57.2
/spindle/DC_MOTOR_GND_1: J16.1, Q1.3 (S), R48.1
/spindle/DC_MOTOR_GND_2: J20.1, Q3.3 (S), R58.1
GNDD: U12.7, U13.2, U13.4, U15.2, U15.4; also elsewhere on the board
unnamed: C21.1, R53.1, R54.2
unnamed: C22.1, R54.1, U14.5 (+)
unnamed: D2.1 (K), R51.2, U12.1
unnamed: J18.1, Q1.2 (D)
unnamed: J21.1, Q3.2 (D)
unnamed: Q1.1 (G), R48.2, U15.7
unnamed: Q3.1 (G), R58.2, U15.5
unnamed: R43.1, U15.1
unnamed: R46.1, U13.1
unnamed: R47.1, U15.8
unnamed: R52.1, R53.2, U13.7
unnamed: R55.1, U13.3
unnamed: R56.1, U15.3
unnamed: R57.1, U15.6
unnamed: U14.1, U14.2 (-)

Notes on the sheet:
BLDC Motor Controller WS55-180/WS55-220
DC Motor 1
DC Motor 2

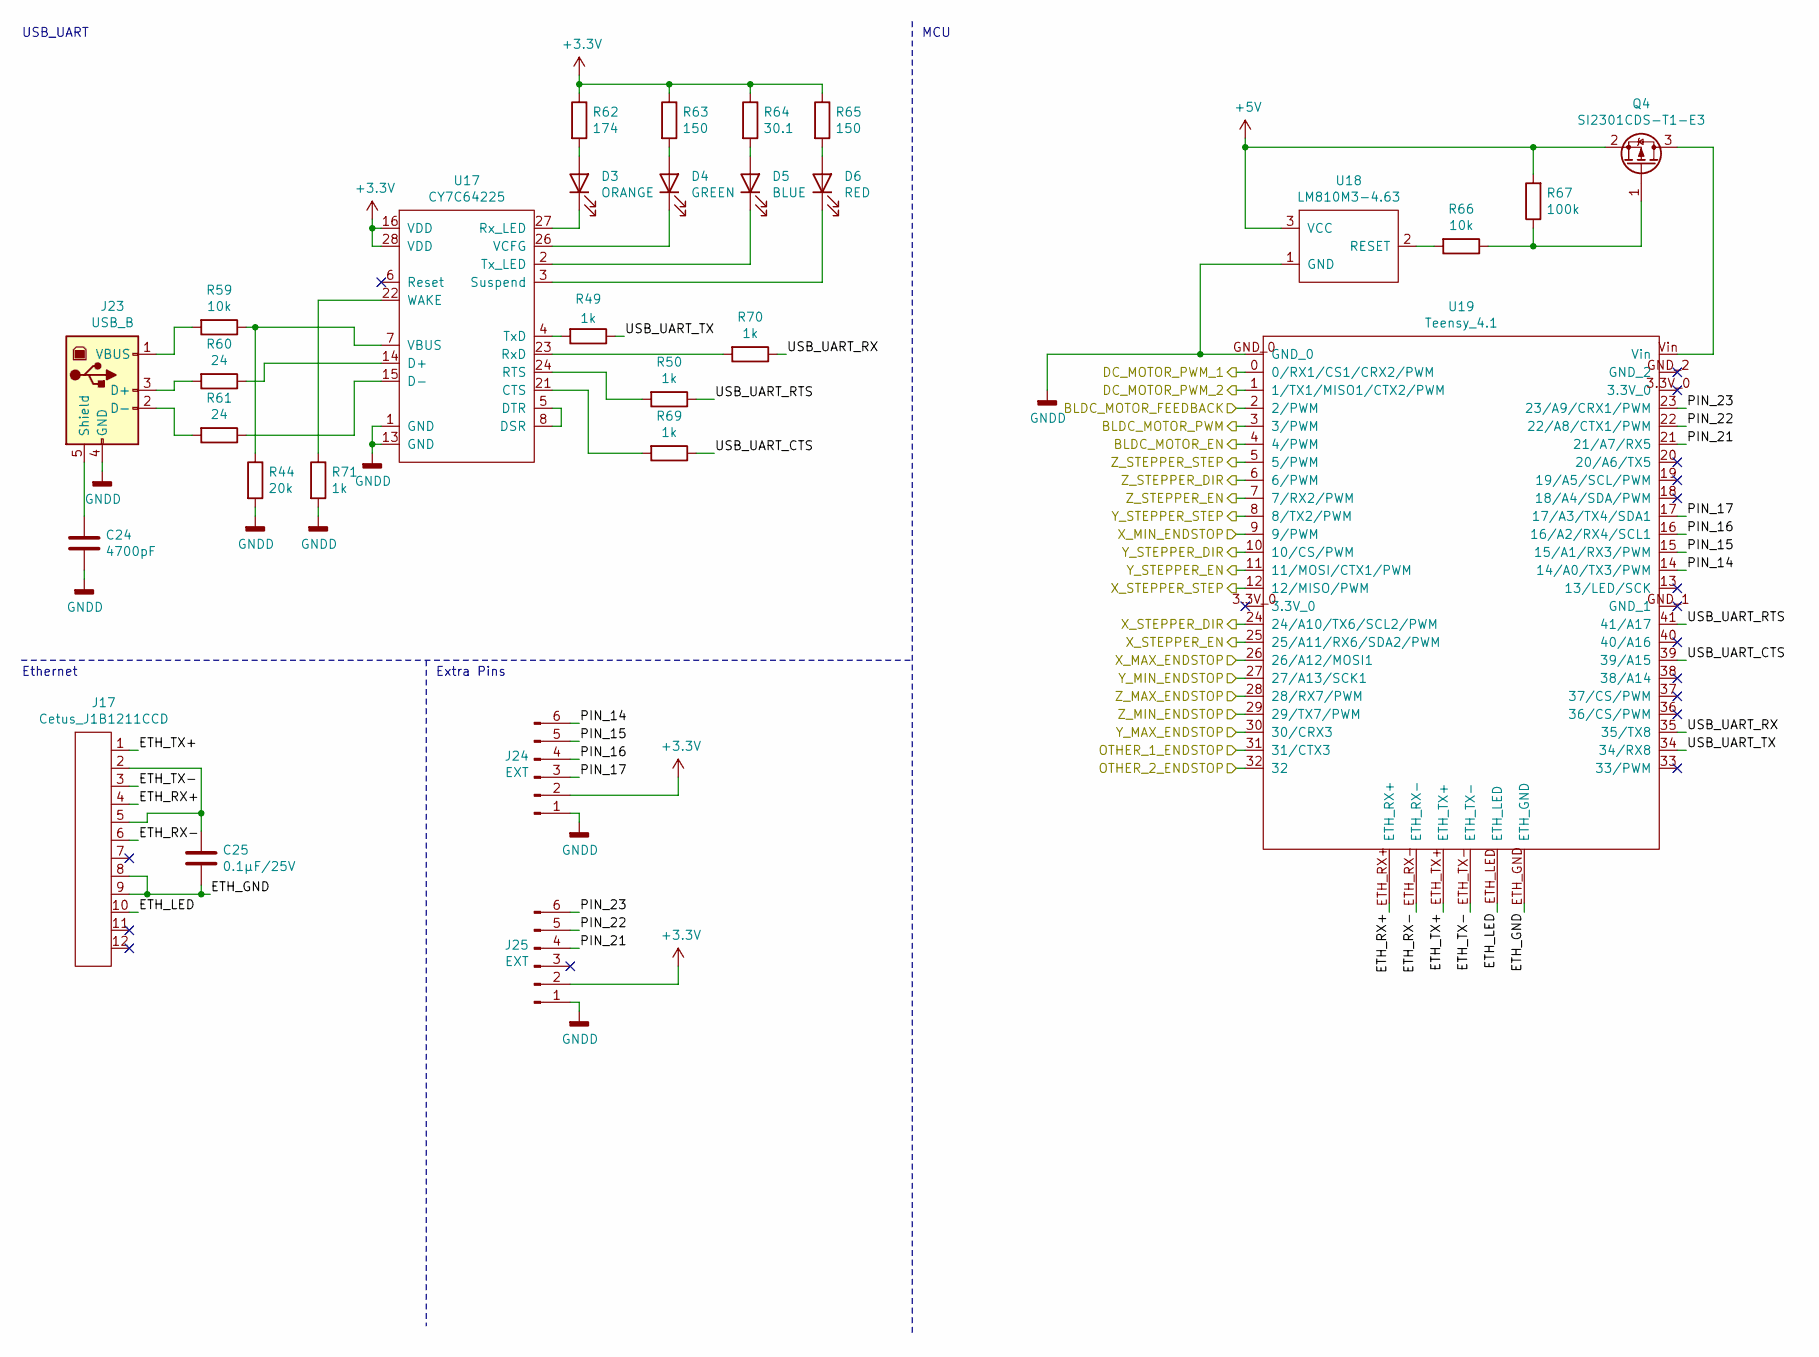
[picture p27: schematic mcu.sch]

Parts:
C24: 4700pF; C_0805_2012Metric
C25: 0.1µF/25V; C_0805_2012Metric
D3: ORANGE; D_0805_2012Metric
D4: GREEN; D_0805_2012Metric
D5: BLUE; D_0805_2012Metric
D6: RED; D_0805_2012Metric
J17: Cetus_J1B1211CCD; Cetus J1B1211CCD
J23: USB_B; USB_B_OST_USB-B1HSxx_Horizontal
J24, J25: EXT; JST_XH_B6B-XH-A_1x06_P2.50mm_Vertical
Q4: SI2301CDS-T1-E3; SOT-23
R44: 20k; R_0805_2012Metric
R49, R50, R69, R70, R71: 1k; R_0805_2012Metric
R59, R66: 10k; R_0805_2012Metric
R60, R61: 24; R_0805_2012Metric
R62: 174; R_0805_2012Metric
R63, R65: 150; R_0805_2012Metric
R64: 30.1; R_0805_2012Metric
R67: 100k; R_0805_2012Metric
U17: CY7C64225; SSOP-28_5.3x10.2mm_P0.65mm
U18: LM810M3-4.63; SOT-23
U19: Teensy_4.1; Teensy 4.1

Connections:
+3V3: J24.2, J25.2, R62.1, R63.1, R64.1, R65.1, U17.16 (VDD), U17.28 (VDD); also elsewhere on the board
+5V: Q4.2 (S), R67.2, U18.3 (VCC); also elsewhere on the board
/endstops/X_MAX: U19.26 (26/A12/MOSI1); also elsewhere on the board
/endstops/X_MIN: U19.9 (9/PWM); also elsewhere on the board
/endstops/Y_MAX: U19.30 (30/CRX3); also elsewhere on the board
/endstops/Y_MIN: U19.27 (27/A13/SCK1); also elsewhere on the board
/endstops/Z_MAX: U19.28 (28/RX7/PWM); also elsewhere on the board
/endstops/Z_MIN: U19.29 (29/TX7/PWM); also elsewhere on the board
/mcu/BLDC_MOTOR_PWM: U19.3 (3/PWM); also elsewhere on the board
/mcu/DC_MOTOR_PWM_1: U19.0 (0/RX1/CS1/CRX2/PWM); also elsewhere on the board
/mcu/DC_MOTOR_PWM_2: U19.1 (1/TX1/MISO1/CTX2/PWM); also elsewhere on the board
/mcu/ETH_GND: C25.2, J17.8, J17.9, U19.ETH_GND
/mcu/ETH_LED: J17.10, U19.ETH_LED
/mcu/ETH_RX+: J17.4, U19.ETH_RX+
/mcu/ETH_RX-: J17.6, U19.ETH_RX-
/mcu/ETH_TX+: J17.1, U19.ETH_TX+
/mcu/ETH_TX-: J17.3, U19.ETH_TX-
/mcu/OTHER_1_ENDSTOP: U19.31 (31/CTX3); also elsewhere on the board
/mcu/OTHER_2_ENDSTOP: U19.32; also elsewhere on the board
/mcu/PIN_14: J24.6, U19.14 (14/A0/TX3/PWM)
/mcu/PIN_15: J24.5, U19.15 (15/A1/RX3/PWM)
/mcu/PIN_16: J24.4, U19.16 (16/A2/RX4/SCL1)
/mcu/PIN_17: J24.3, U19.17 (17/A3/TX4/SDA1)
/mcu/PIN_20: J25.3
/mcu/PIN_21: J25.4, U19.21 (21/A7/RX5)
/mcu/PIN_22: J25.5, U19.22 (22/A8/CTX1/PWM)
/mcu/PIN_23: J25.6, U19.23 (23/A9/CRX1/PWM)
/mcu/USB_UART_CTS: R69.1, U19.39 (39/A15)
/mcu/USB_UART_RTS: R50.1, U19.41 (41/A17)
/mcu/USB_UART_RX: R70.1, U19.35 (35/TX8)
/mcu/USB_UART_TX: R49.1, U19.34 (34/RX8)
/spindle/BLDC_EN: U19.4 (4/PWM); also elsewhere on the board
/spindle/BLDC_FEEDBACK: U19.2 (2/PWM); also elsewhere on the board
/steppers/X_DIR: U19.24 (24/A10/TX6/SCL2/PWM); also elsewhere on the board
/steppers/X_EN: U19.25 (25/A11/RX6/SDA2/PWM); also elsewhere on the board
/steppers/X_STEP: U19.12 (12/MISO/PWM); also elsewhere on the board
/steppers/Y_DIR: U19.10 (10/CS/PWM); also elsewhere on the board
/steppers/Y_EN: U19.11 (11/MOSI/CTX1/PWM); also elsewhere on the board
/steppers/Y_STEP: U19.8 (8/TX2/PWM); also elsewhere on the board
/steppers/Z_DIR: U19.6 (6/PWM); also elsewhere on the board
/steppers/Z_EN: U19.7 (7/RX2/PWM); also elsewhere on the board
/steppers/Z_STEP: U19.5 (5/PWM); also elsewhere on the board
GNDD: C24.2, J23.4 (GND), J24.1, J25.1, R44.2, R71.2, U17.1 (GND), U17.13 (GND), U18.1 (GND), U19.GND_0; also elsewhere on the board
unnamed: C24.1, J23.5 (Shield)
unnamed: C25.1, J17.2, J17.5
unnamed: D3.1 (K), U17.27 (Rx_LED)
unnamed: D3.2 (A), R62.2
unnamed: D4.1 (K), U17.26 (VCFG)
unnamed: D4.2 (A), R63.2
unnamed: D5.1 (K), U17.2 (Tx_LED)
unnamed: D5.2 (A), R64.2
unnamed: D6.1 (K), U17.3 (Suspend)
unnamed: D6.2 (A), R65.2
unnamed: J23.1 (VBUS), R59.2
unnamed: J23.2 (D-), R61.2
unnamed: J23.3 (D+), R60.2
unnamed: Q4.1 (G), R66.1, R67.1
unnamed: Q4.3 (D), U19.Vin
unnamed: R44.1, R59.1, U17.7 (VBUS)
unnamed: R49.2, U17.4 (TxD)
unnamed: R50.2, U17.24 (RTS)
unnamed: R60.1, U17.14 (D+)
unnamed: R61.1, U17.15 (D-)
unnamed: R66.2, U18.2 (RESET)
unnamed: R69.2, U17.21 (CTS)
unnamed: R70.2, U17.23 (RxD)
unnamed: R71.1, U17.22 (WAKE)
unnamed: U17.5 (DTR), U17.8 (DSR)

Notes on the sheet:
USB_UART
Ethernet
MCU
Extra Pins

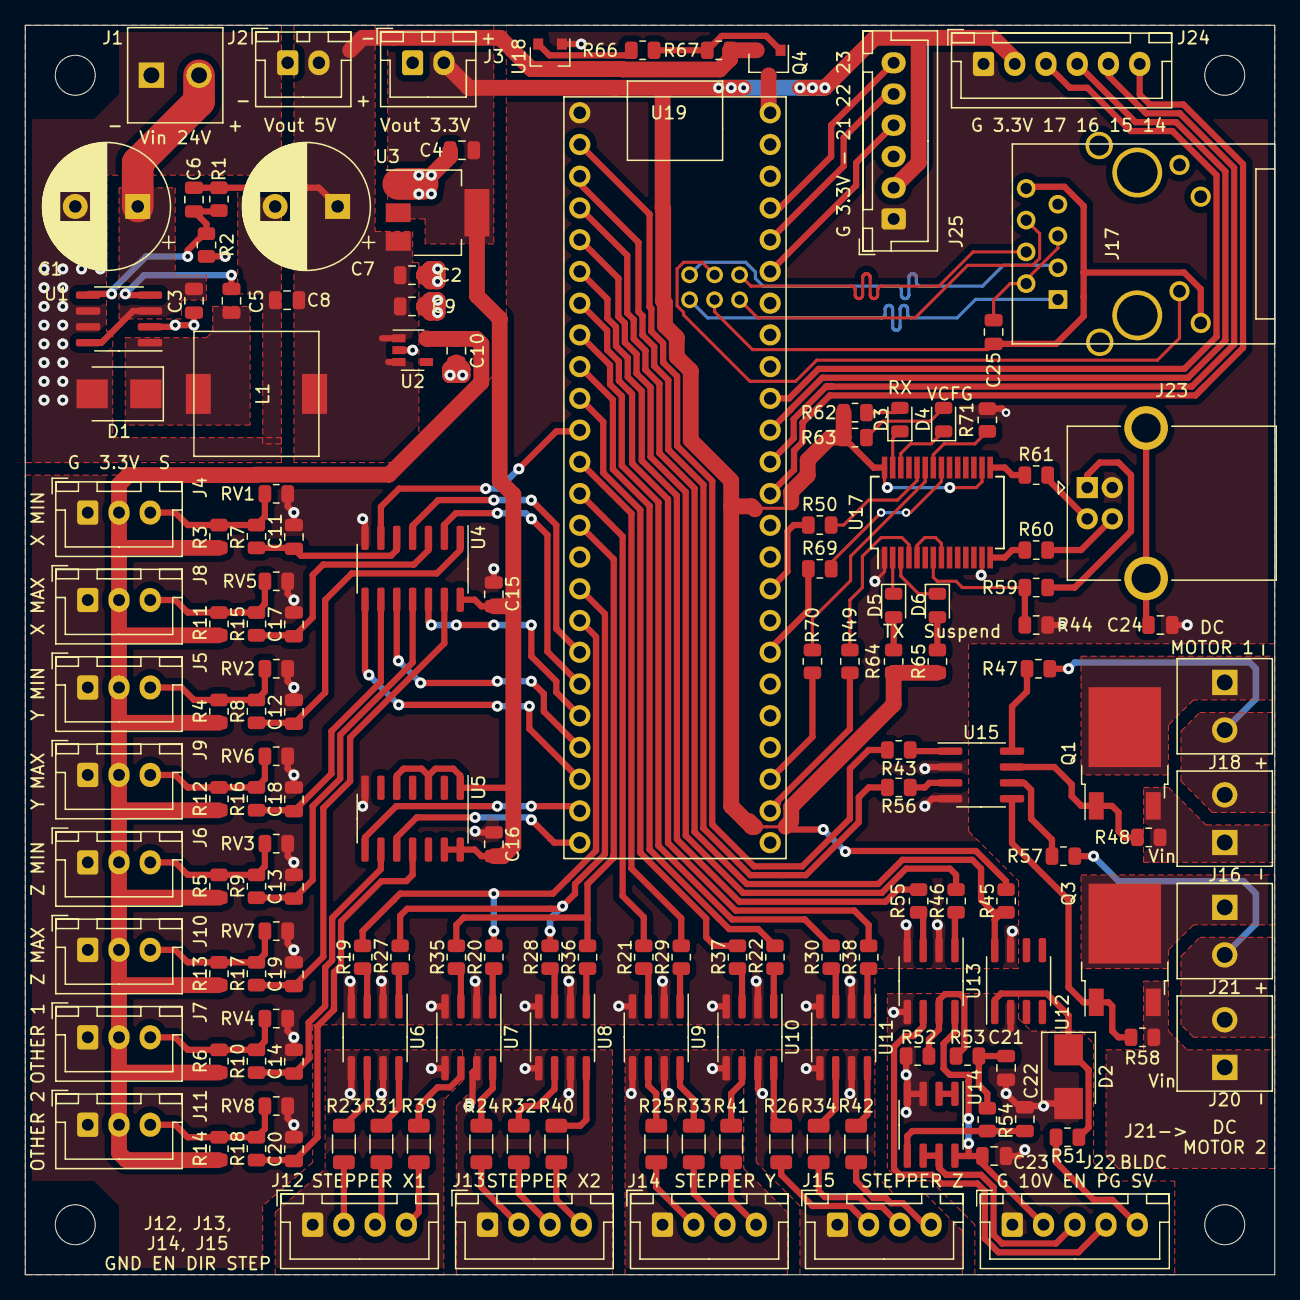
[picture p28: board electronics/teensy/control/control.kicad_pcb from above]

Board: 2 copper layers, 100.0 x 100.0 mm, 156 parts (1 on the bottom side), 153 nets.

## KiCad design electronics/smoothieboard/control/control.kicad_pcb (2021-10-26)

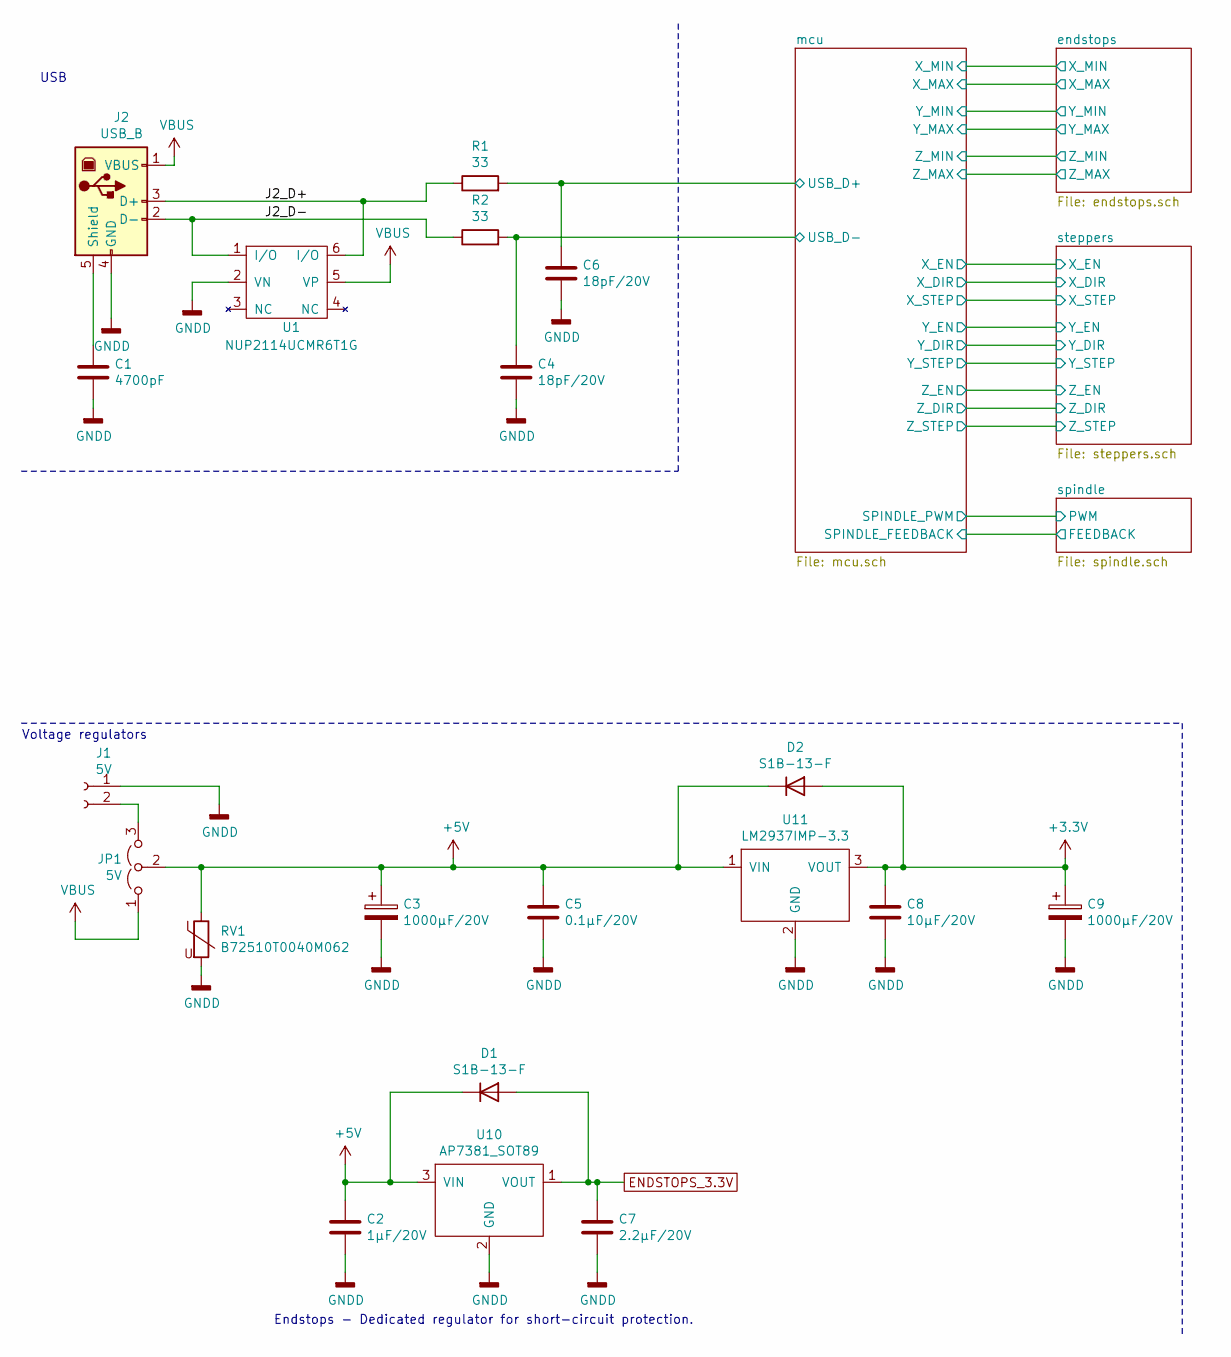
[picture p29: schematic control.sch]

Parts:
C1: 4700pF; C_0805_2012Metric
C2: 1µF/20V; C_0805_2012Metric
C3, C9: 1000µF/20V; CP_Radial_D10.0mm_P5.00mm
C4, C6: 18pF/20V; C_0805_2012Metric
C5: 0.1µF/20V; C_0805_2012Metric
C7: 2.2µF/20V; C_0805_2012Metric
C8: 10µF/20V; C_0805_2012Metric
D1, D2: S1B-13-F; D_SMA
J1: 5V; EBWA-02-B
J2: USB_B; USB_B_OST_USB-B1HSxx_Horizontal
JP1: 5V; PinHeader_1x03_P2.54mm_Vertical
R1, R2: 33; R_0805_2012Metric
RV1: B72510T0040M062; R_0805_2012Metric
U1: NUP2114UCMR6T1G; SOT-23-6
U10: AP7381_SOT89; SOT-89-3
U11: LM2937IMP-3.3; SOT-223-3_TabPin2

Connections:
+3V3: C8.1, C9.1, D2.2 (A), U11.3 (VOUT); also elsewhere on the board
+5V: C2.1, C3.1, C5.1, D1.1 (K), D2.1 (K), JP1.2 (C), RV1.1, U10.3 (VIN), U11.1 (VIN)
/J2_D+: J2.3 (D+), R1.1, U1.6 (I/O)
/J2_D-: J2.2 (D-), R2.1, U1.1 (I/O)
/mcu/USB_D+: C6.1, R1.2; also elsewhere on the board
/mcu/USB_D-: C4.1, R2.2; also elsewhere on the board
ENDSTOPS_3.3V: C7.1, D1.2 (A), U10.1 (VOUT); also elsewhere on the board
GNDD: C1.2, C2.2, C3.2, C4.2, C5.2, C6.2, C7.2, C8.2, C9.2, J1.1, J2.4 (GND), RV1.2, U1.2 (VN), U10.2 (GND), U11.2 (GND); also elsewhere on the board
unnamed: C1.1, J2.5 (Shield)
unnamed: J1.2, JP1.3 (B)
VBUS: J2.1 (VBUS), JP1.1 (A), U1.5 (VP)

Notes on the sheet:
Endstops - Dedicated regulator for short-circuit protection.
USB
Voltage regulators

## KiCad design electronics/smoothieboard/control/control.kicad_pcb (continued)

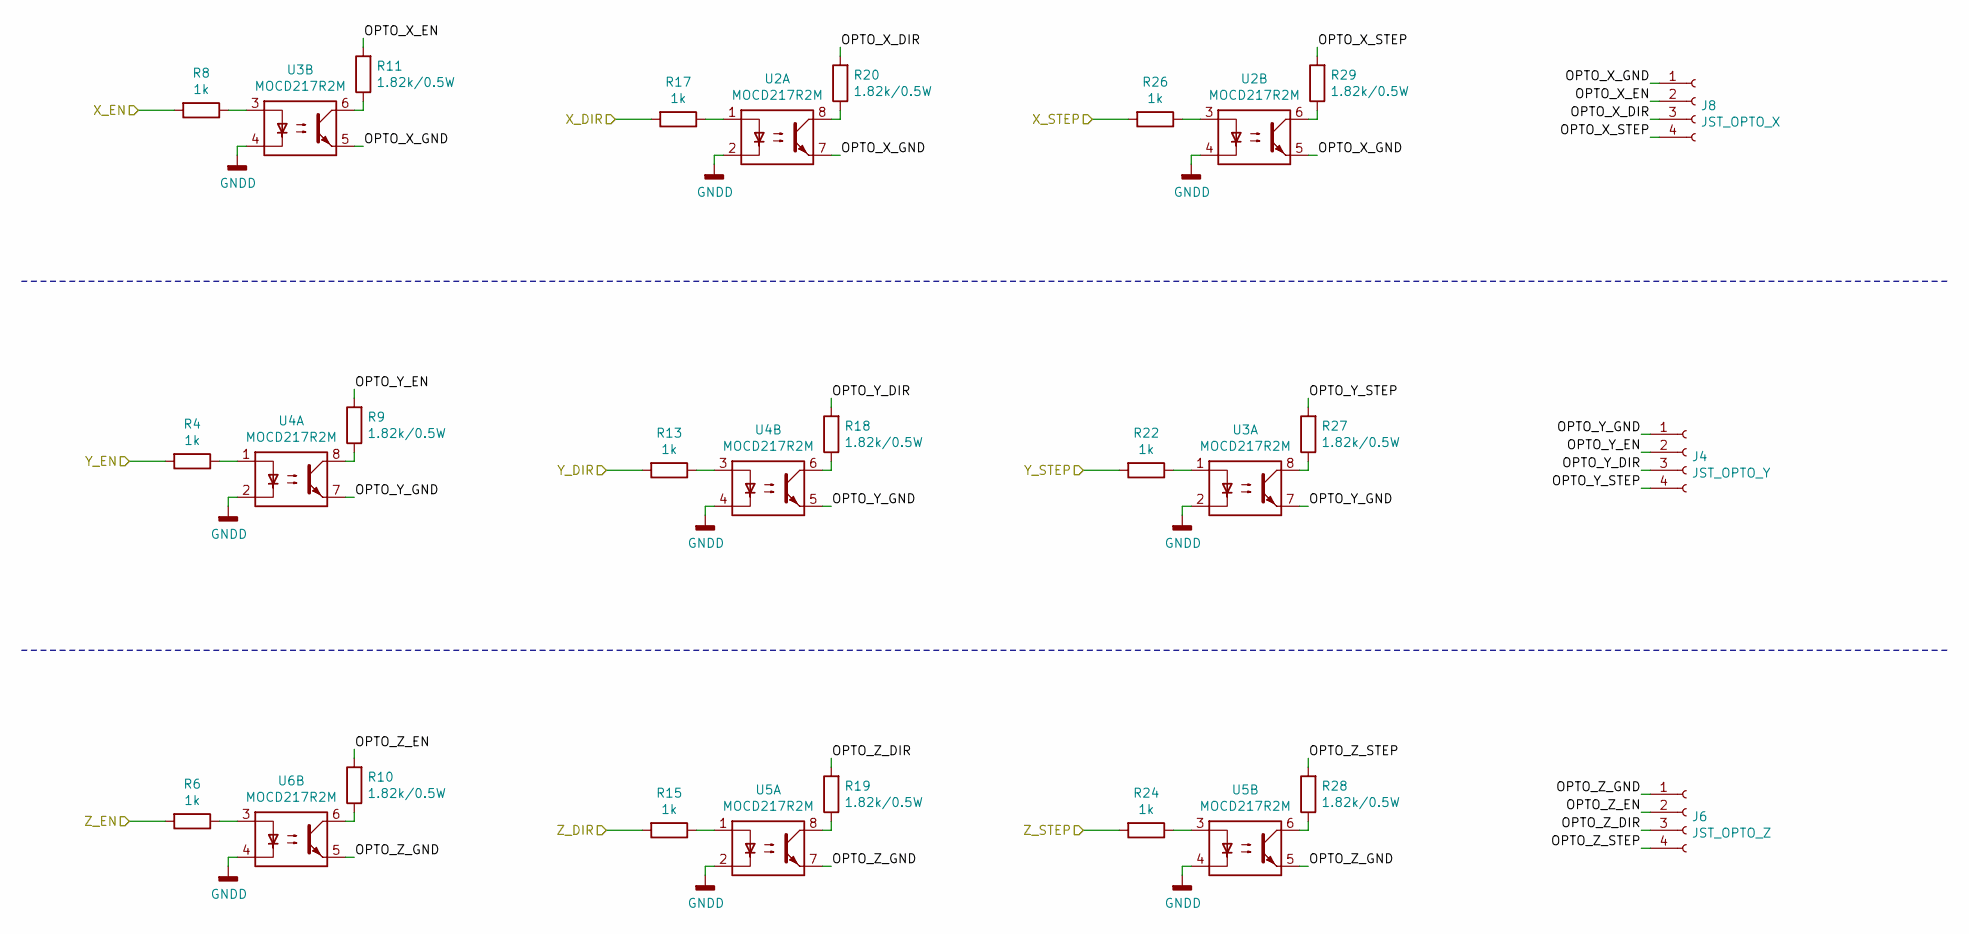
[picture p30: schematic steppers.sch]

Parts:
J4: JST_OPTO_Y; JST_XH_B4B-XH-A_1x04_P2.50mm_Vertical
J6: JST_OPTO_Z; JST_XH_B4B-XH-A_1x04_P2.50mm_Vertical
J8: JST_OPTO_X; JST_XH_B4B-XH-A_1x04_P2.50mm_Vertical
R4, R6, R8, R13, R15, R17, R22, R24, R26: 1k; R_0805_2012Metric
R9, R10, R11, R18, R19, R20, R27, R28, R29: 1.82k/0.5W; R_1210_3225Metric
U2, U3, U4, U5, U6: MOCD217R2M; SOIC-8_3.9x4.9mm_P1.27mm

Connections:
/mcu/X_DIR: R17.2; also elsewhere on the board
/mcu/X_EN: R8.2; also elsewhere on the board
/mcu/X_STEP: R26.2; also elsewhere on the board
/mcu/Y_DIR: R13.2; also elsewhere on the board
/mcu/Y_EN: R4.2; also elsewhere on the board
/mcu/Y_STEP: R22.2; also elsewhere on the board
/mcu/Z_DIR: R15.2; also elsewhere on the board
/mcu/Z_EN: R6.2; also elsewhere on the board
/mcu/Z_STEP: R24.2; also elsewhere on the board
/steppers/OPTO_X_DIR: J8.3, R20.2
/steppers/OPTO_X_EN: J8.2, R11.2
/steppers/OPTO_X_GND: J8.1, U2.5, U2.7, U3.5
/steppers/OPTO_X_STEP: J8.4, R29.2
/steppers/OPTO_Y_DIR: J4.3, R18.2
/steppers/OPTO_Y_EN: J4.2, R9.2
/steppers/OPTO_Y_GND: J4.1, U3.7, U4.5, U4.7
/steppers/OPTO_Y_STEP: J4.4, R27.2
/steppers/OPTO_Z_DIR: J6.3, R19.2
/steppers/OPTO_Z_EN: J6.2, R10.2
/steppers/OPTO_Z_GND: J6.1, U5.5, U5.7, U6.5
/steppers/OPTO_Z_STEP: J6.4, R28.2
GNDD: U2.2, U2.4, U3.2, U3.4, U4.2, U4.4, U5.2, U5.4, U6.4; also elsewhere on the board
unnamed: R4.1, U4.1
unnamed: R6.1, U6.3
unnamed: R8.1, U3.3
unnamed: R9.1, U4.8
unnamed: R10.1, U6.6
unnamed: R11.1, U3.6
unnamed: R13.1, U4.3
unnamed: R15.1, U5.1
unnamed: R17.1, U2.1
unnamed: R18.1, U4.6
unnamed: R19.1, U5.8
unnamed: R20.1, U2.8
unnamed: R22.1, U3.1
unnamed: R24.1, U5.3
unnamed: R26.1, U2.3
unnamed: R27.1, U3.8
unnamed: R28.1, U5.6
unnamed: R29.1, U2.6

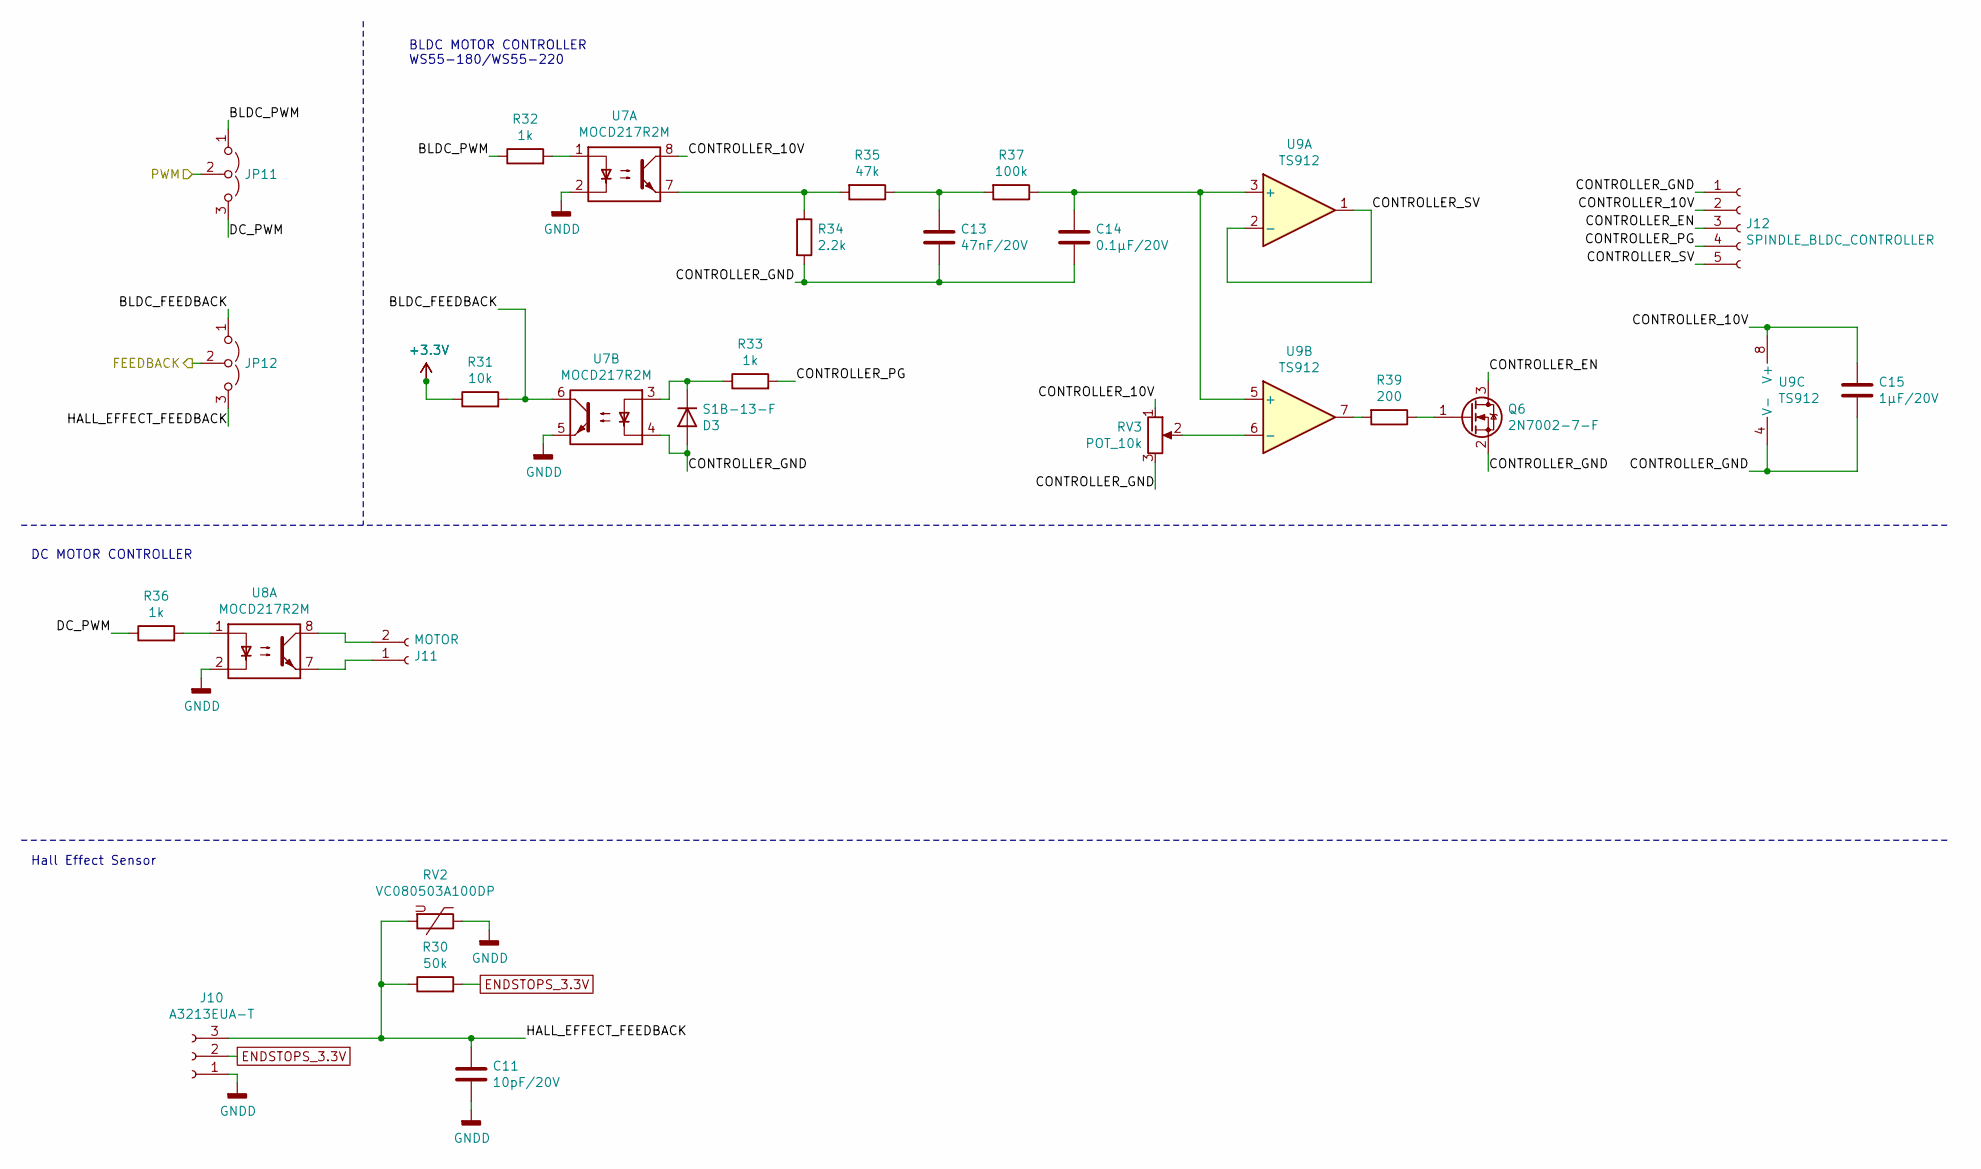
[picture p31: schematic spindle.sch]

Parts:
C11: 10pF/20V; C_0805_2012Metric
C13: 47nF/20V; C_0805_2012Metric
C14: 0.1µF/20V; C_0805_2012Metric
C15: 1µF/20V; C_0805_2012Metric
D3: S1B-13-F; D_SMA
J10: A3213EUA-T; JST_XH_B3B-XH-A_1x03_P2.50mm_Vertical
J11: MOTOR; JST_XH_B2B-XH-A_1x02_P2.50mm_Vertical
J12: SPINDLE_BLDC_CONTROLLER; JST_XH_B5B-XH-A_1x05_P2.50mm_Vertical
JP11, JP12: Jumper_3_Open; PinHeader_1x03_P2.54mm_Vertical
Q6: 2N7002-7-F; SOT-23
R30: 50k; R_0805_2012Metric
R31: 10k; R_0805_2012Metric
R32, R33, R36: 1k; R_0805_2012Metric
R34: 2.2k; R_0805_2012Metric
R35: 47k; R_0805_2012Metric
R37: 100k; R_0805_2012Metric
R39: 200; R_0805_2012Metric
RV2: VC080503A100DP; R_0805_2012Metric
RV3: POT_10k; Potentiometer_Bourns_3266Y_Vertical
U7, U8: MOCD217R2M; SOIC-8_3.9x4.9mm_P1.27mm
U9: TS912; SOIC-8_3.9x4.9mm_P1.27mm

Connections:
+3V3: R31.1; also elsewhere on the board
/spindle/BLDC_FEEDBACK: JP12.1 (A), R31.2, U7.6
/spindle/BLDC_PWM: JP11.1 (A), R32.1
/spindle/CONTROLLER_10V: C15.1, J12.2, RV3.1, U7.8, U9.8 (V+)
/spindle/CONTROLLER_EN: J12.3, Q6.3 (D)
/spindle/CONTROLLER_GND: C13.2, C14.2, C15.2, D3.2 (A), J12.1, Q6.2 (S), R34.2, RV3.3, U7.4, U9.4 (V-)
/spindle/CONTROLLER_PG: J12.4, R33.2
/spindle/CONTROLLER_SV: J12.5, U9.1, U9.2 (-)
/spindle/DC_PWM: JP11.3 (B), R36.1
/spindle/FEEDBACK: JP12.2 (C); also elsewhere on the board
/spindle/HALL_EFFECT_FEEDBACK: C11.1, J10.3, JP12.3 (B), R30.1, RV2.2
/spindle/PWM: JP11.2 (C); also elsewhere on the board
ENDSTOPS_3.3V: J10.2, R30.2; also elsewhere on the board
GNDD: C11.2, J10.1, RV2.1, U7.2, U7.5, U8.2; also elsewhere on the board
unnamed: C13.1, R35.1, R37.2
unnamed: C14.1, R37.1, U9.3 (+), U9.5 (+)
unnamed: D3.1 (K), R33.1, U7.3
unnamed: J11.1, U8.7
unnamed: J11.2, U8.8
unnamed: Q6.1 (G), R39.1
unnamed: R32.2, U7.1
unnamed: R34.1, R35.2, U7.7
unnamed: R36.2, U8.1
unnamed: R39.2, U9.7
unnamed: RV3.2, U9.6 (-)

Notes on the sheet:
BLDC MOTOR CONTROLLER WS55-180/WS55-220
DC MOTOR CONTROLLER
Hall Effect Sensor

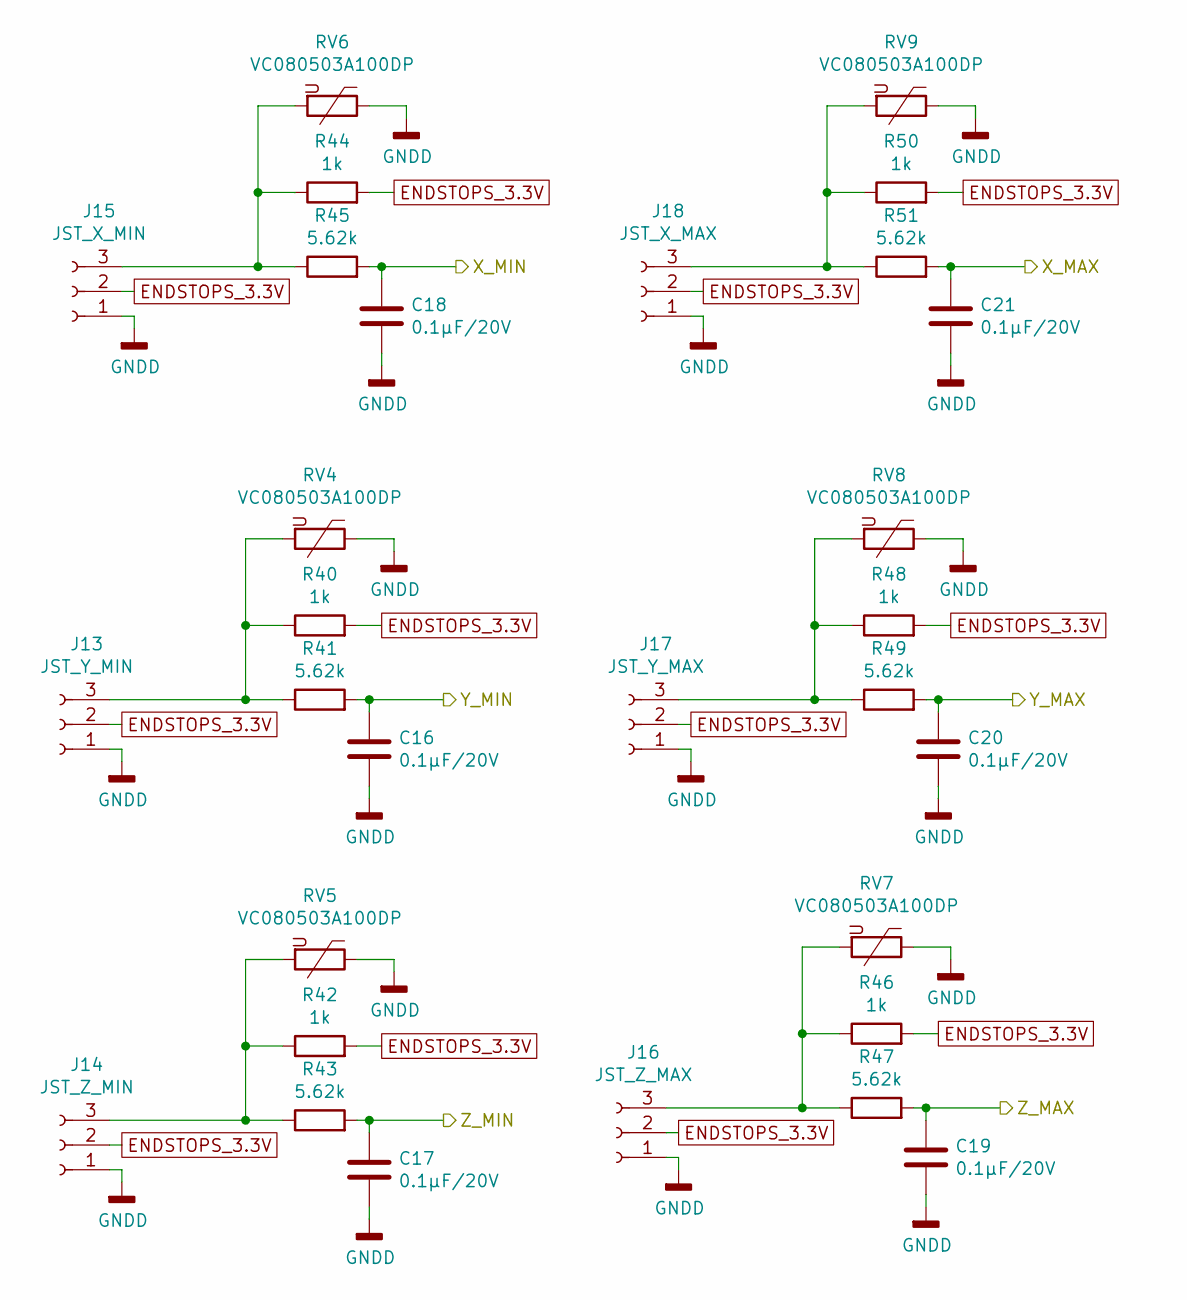
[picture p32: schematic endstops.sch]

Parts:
C16, C17, C18, C19, C20, C21: 0.1µF/20V; C_0805_2012Metric
J13: JST_Y_MIN; JST_XH_B3B-XH-A_1x03_P2.50mm_Vertical
J14: JST_Z_MIN; JST_XH_B3B-XH-A_1x03_P2.50mm_Vertical
J15: JST_X_MIN; JST_XH_B3B-XH-A_1x03_P2.50mm_Vertical
J16: JST_Z_MAX; JST_XH_B3B-XH-A_1x03_P2.50mm_Vertical
J17: JST_Y_MAX; JST_XH_B3B-XH-A_1x03_P2.50mm_Vertical
J18: JST_X_MAX; JST_XH_B3B-XH-A_1x03_P2.50mm_Vertical
R40, R42, R44, R46, R48, R50: 1k; R_0805_2012Metric
R41, R43, R45, R47, R49, R51: 5.62k; R_0805_2012Metric
RV4, RV5, RV6, RV7, RV8, RV9: VC080503A100DP; R_0805_2012Metric

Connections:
/endstops/X_MAX: C21.1, R51.2; also elsewhere on the board
/endstops/X_MIN: C18.1, R45.2; also elsewhere on the board
/endstops/Y_MAX: C20.1, R49.2; also elsewhere on the board
/endstops/Y_MIN: C16.1, R41.2; also elsewhere on the board
/endstops/Z_MAX: C19.1, R47.2; also elsewhere on the board
/endstops/Z_MIN: C17.1, R43.2; also elsewhere on the board
ENDSTOPS_3.3V: J13.2, J14.2, J15.2, J16.2, J17.2, J18.2, R40.2, R42.2, R44.2, R46.2, R48.2, R50.2; also elsewhere on the board
GNDD: C16.2, C17.2, C18.2, C19.2, C20.2, C21.2, J13.1, J14.1, J15.1, J16.1, J17.1, J18.1, RV4.1, RV5.1, RV6.1, RV7.1, RV8.1, RV9.1; also elsewhere on the board
unnamed: J13.3, R40.1, R41.1, RV4.2
unnamed: J14.3, R42.1, R43.1, RV5.2
unnamed: J15.3, R44.1, R45.1, RV6.2
unnamed: J16.3, R46.1, R47.1, RV7.2
unnamed: J17.3, R48.1, R49.1, RV8.2
unnamed: J18.3, R50.1, R51.1, RV9.2

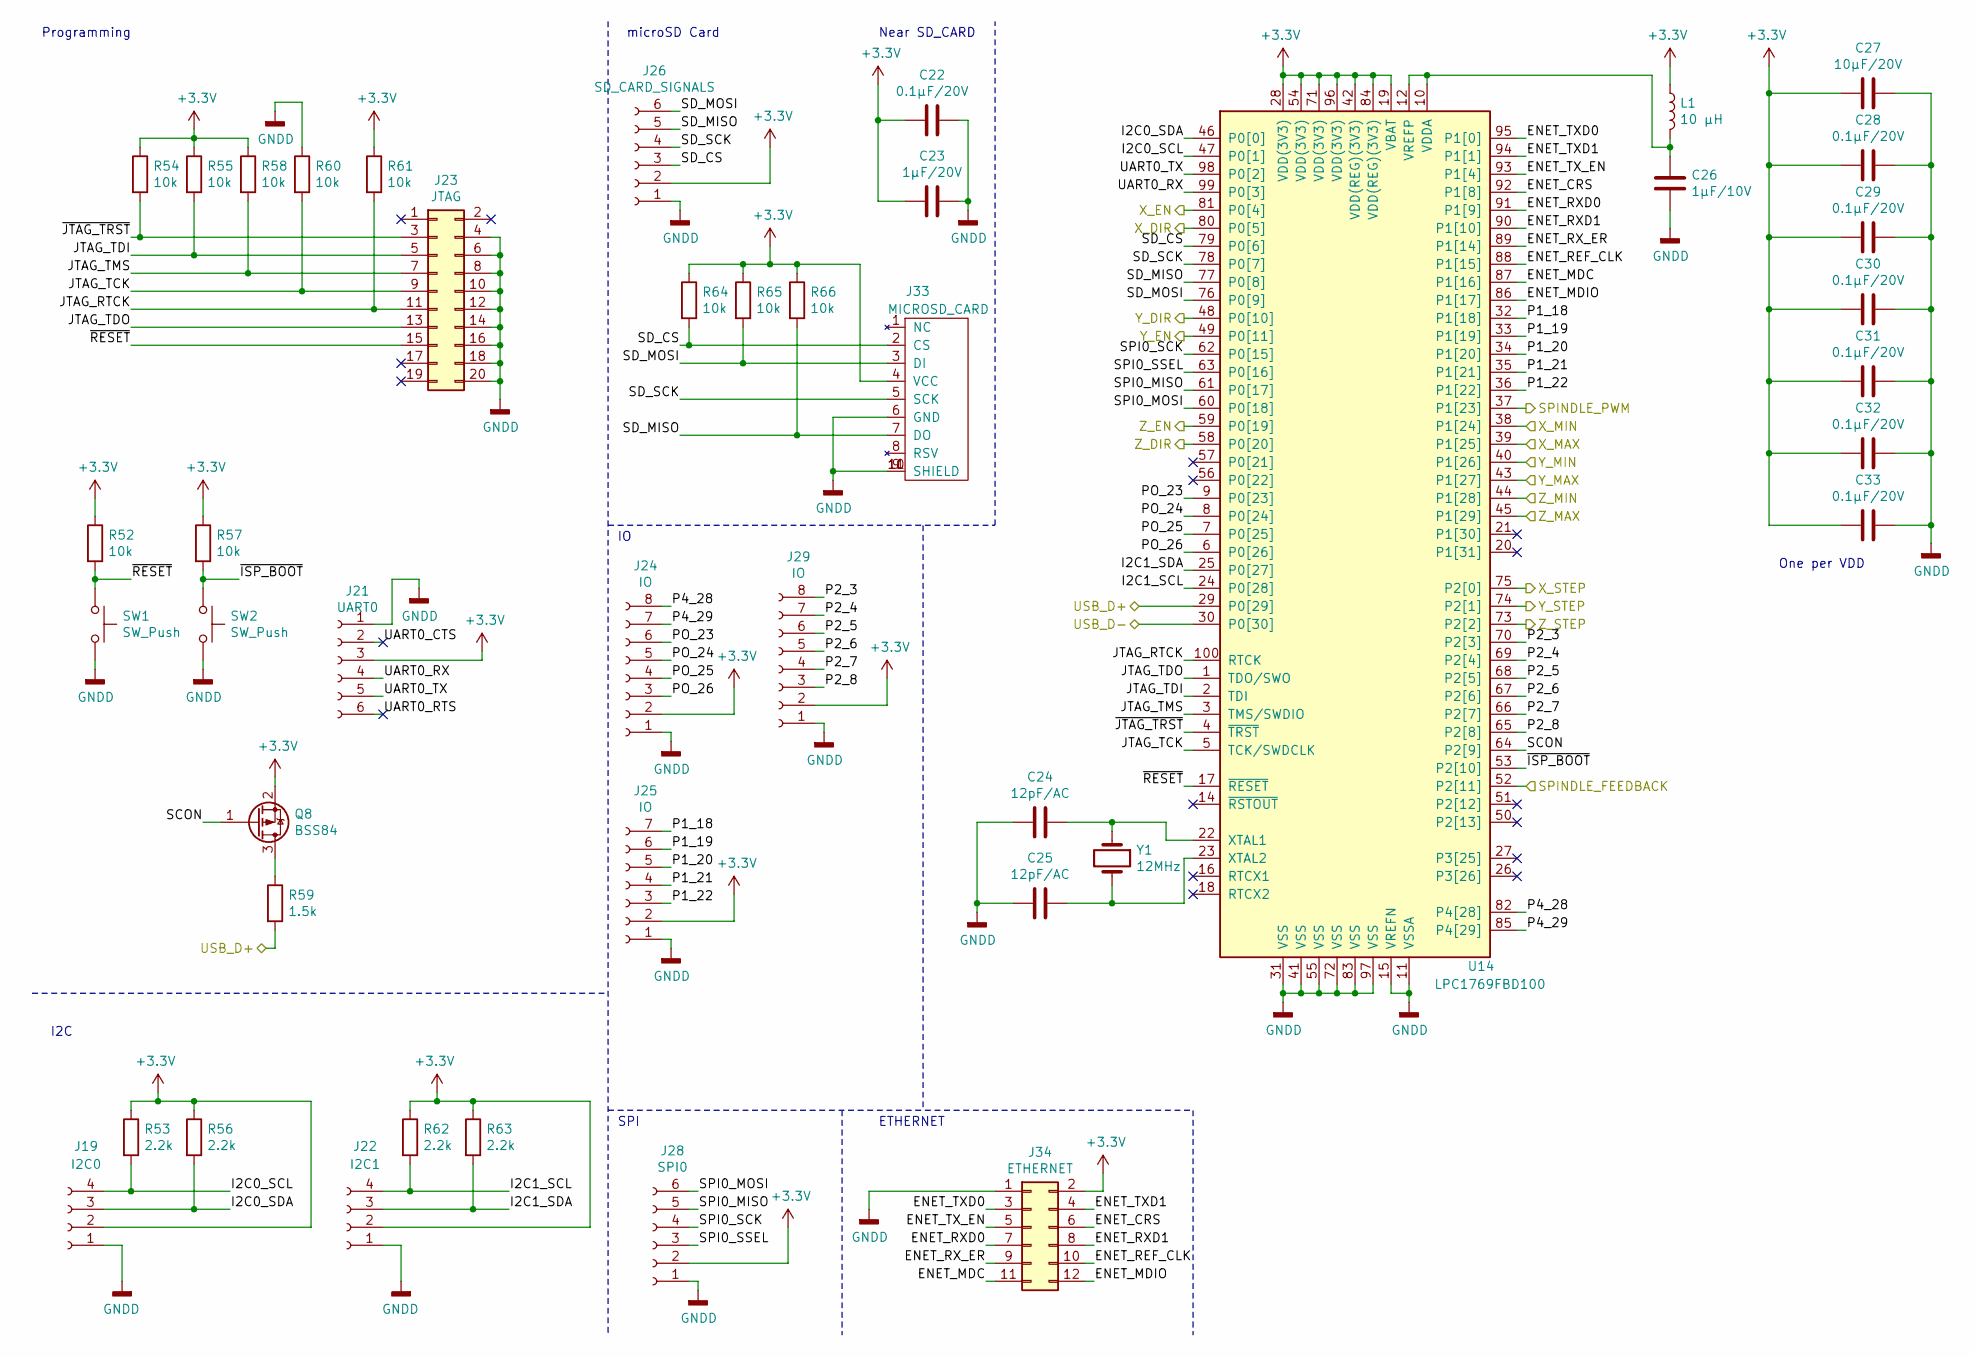
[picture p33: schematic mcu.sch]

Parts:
C22, C28, C29, C30, C31, C32, C33: 0.1µF/20V; C_0805_2012Metric
C23: 1µF/20V; C_0805_2012Metric
C24, C25: 12pF/AC; C_0805_2012Metric
C26: 1µF/10V; C_0805_2012Metric
C27: 10µF/20V; C_0805_2012Metric
J19: I2C0; JST_XH_B4B-XH-A_1x04_P2.50mm_Vertical
J21: UART0; JST_XH_B6B-XH-A_1x06_P2.50mm_Vertical
J22: I2C1; JST_XH_B4B-XH-A_1x04_P2.50mm_Vertical
J23: JTAG; IDC-Header_2x10_P2.54mm_Vertical
J24, J29: IO; JST_XH_B8B-XH-A_1x08_P2.50mm_Vertical
J25: IO; JST_XH_B7B-XH-A_1x07_P2.50mm_Vertical
J26: SD_CARD_SIGNALS; JST_XH_B6B-XH-A_1x06_P2.50mm_Vertical
J28: SPI0; JST_XH_B6B-XH-A_1x06_P2.50mm_Vertical
J33: MICROSD_CARD; microSD_HC_Hirose_DM3D-SF
J34: ETHERNET; IDC-Header_2x06_P2.54mm_Vertical
L1: 10 µH; L_0805_2012Metric
Q8: BSS84; SOT-23
R52, R54, R55, R57, R58, R60, R61, R64, R65, R66: 10k; R_0805_2012Metric
R53, R56, R62, R63: 2.2k; R_0805_2012Metric
R59: 1.5k; R_0805_2012Metric
SW1, SW2: SW_Push; SW_PUSH_6mm_H5mm
U14: LPC1769FBD100; LQFP-100_14x14mm_P0.5mm
Y1: 12MHz; Crystal_SMD_Abracon_ABM3-2Pin_5.0x3.2mm

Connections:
+3V3: C22.1, C23.1, C27.2, C28.2, C29.2, C30.2, C31.2, C32.2, C33.2, J19.2, J21.3, J22.2, J24.2, J25.2, J26.2, J28.2, J29.2, J33.4 (VCC), J34.2, L1.1, Q8.2 (S), R52.1, R53.1, R54.1, R55.1, R56.1, R57.1, R58.1, R61.1, R62.1, R63.1, R64.1, R65.1, R66.1, U14.19 (VBAT), U14.28 (VDD(3V3)), U14.42 (VDD(REG)(3V3)), U14.54 (VDD(3V3)), U14.71 (VDD(3V3)), U14.84 (VDD(REG)(3V3)), U14.96 (VDD(3V3)); also elsewhere on the board
/endstops/X_MAX: U14.39 (P1[25]); also elsewhere on the board
/endstops/X_MIN: U14.38 (P1[24]); also elsewhere on the board
/endstops/Y_MAX: U14.43 (P1[27]); also elsewhere on the board
/endstops/Y_MIN: U14.40 (P1[26]); also elsewhere on the board
/endstops/Z_MAX: U14.45 (P1[29]); also elsewhere on the board
/endstops/Z_MIN: U14.44 (P1[28]); also elsewhere on the board
/mcu/ENET_CRS: J34.6, U14.92 (P1[8])
/mcu/ENET_MDC: J34.11, U14.87 (P1[16])
/mcu/ENET_MDIO: J34.12, U14.86 (P1[17])
/mcu/ENET_REF_CLK: J34.10, U14.88 (P1[15])
/mcu/ENET_RXD0: J34.7, U14.91 (P1[9])
/mcu/ENET_RXD1: J34.8, U14.90 (P1[10])
/mcu/ENET_RX_ER: J34.9, U14.89 (P1[14])
/mcu/ENET_TXD0: J34.3, U14.95 (P1[0])
/mcu/ENET_TXD1: J34.4, U14.94 (P1[1])
/mcu/ENET_TX_EN: J34.5, U14.93 (P1[4])
/mcu/I2C0_SCL: J19.4, R53.2, U14.47 (P0[1])
/mcu/I2C0_SDA: J19.3, R56.2, U14.46 (P0[0])
/mcu/I2C1_SCL: J22.4, R62.2, U14.24 (P0[28])
/mcu/I2C1_SDA: J22.3, R63.2, U14.25 (P0[27])
/mcu/JTAG_RTCK: J23.11, R61.2, U14.100 (RTCK)
/mcu/JTAG_TCK: J23.9, R60.2, U14.5 (TCK/SWDCLK)
/mcu/JTAG_TDI: J23.5, R55.2, U14.2 (TDI)
/mcu/JTAG_TDO: J23.13, U14.1 (TDO/SWO)
/mcu/JTAG_TMS: J23.7, R58.2, U14.3 (TMS/SWDIO)
/mcu/P1_18: J25.7, U14.32 (P1[18])
/mcu/P1_19: J25.6, U14.33 (P1[19])
/mcu/P1_20: J25.5, U14.34 (P1[20])
/mcu/P1_21: J25.4, U14.35 (P1[21])
/mcu/P1_22: J25.3, U14.36 (P1[22])
/mcu/P2_3: J29.8, U14.70 (P2[3])
/mcu/P2_4: J29.7, U14.69 (P2[4])
/mcu/P2_5: J29.6, U14.68 (P2[5])
/mcu/P2_6: J29.5, U14.67 (P2[6])
/mcu/P2_7: J29.4, U14.66 (P2[7])
/mcu/P2_8: J29.3, U14.65 (P2[8])
/mcu/P4_28: J24.8, U14.82 (P4[28])
/mcu/P4_29: J24.7, U14.85 (P4[29])
/mcu/PO_23: J24.6, U14.9 (P0[23])
/mcu/PO_24: J24.5, U14.8 (P0[24])
/mcu/PO_25: J24.4, U14.7 (P0[25])
/mcu/PO_26: J24.3, U14.6 (P0[26])
/mcu/SCON: Q8.1 (G), U14.64 (P2[9])
/mcu/SD_CS: J26.3, J33.2 (CS), R64.2, U14.79 (P0[6])
/mcu/SD_MISO: J26.5, J33.7 (DO), R66.2, U14.77 (P0[8])
/mcu/SD_MOSI: J26.6, J33.3 (DI), R65.2, U14.76 (P0[9])
/mcu/SD_SCK: J26.4, J33.5 (SCK), U14.78 (P0[7])
/mcu/SPI0_MISO: J28.5, U14.61 (P0[17])
/mcu/SPI0_MOSI: J28.6, U14.60 (P0[18])
/mcu/SPI0_SCK: J28.4, U14.62 (P0[15])
/mcu/SPI0_SSEL: J28.3, U14.63 (P0[16])
/mcu/UART0_CTS: J21.2
/mcu/UART0_RTS: J21.6
/mcu/UART0_RX: J21.4, U14.99 (P0[3])
/mcu/UART0_TX: J21.5, U14.98 (P0[2])
/mcu/USB_D+: R59.2, U14.29 (P0[29]); also elsewhere on the board
/mcu/USB_D-: U14.30 (P0[30]); also elsewhere on the board
/mcu/X_DIR: U14.80 (P0[5]); also elsewhere on the board
/mcu/X_EN: U14.81 (P0[4]); also elsewhere on the board
/mcu/X_STEP: U14.75 (P2[0]); also elsewhere on the board
/mcu/Y_DIR: U14.48 (P0[10]); also elsewhere on the board
/mcu/Y_EN: U14.49 (P0[11]); also elsewhere on the board
/mcu/Y_STEP: U14.74 (P2[1]); also elsewhere on the board
/mcu/Z_DIR: U14.58 (P0[20]); also elsewhere on the board
/mcu/Z_EN: U14.59 (P0[19]); also elsewhere on the board
/mcu/Z_STEP: U14.73 (P2[2]); also elsewhere on the board
/mcu/~ISP_BOOT: R57.2, SW2.1, U14.53 (P2[10])
/mcu/~JTAG_TRST: J23.3, R54.2, U14.4 (~TRST~)
/mcu/~RESET: J23.15, R52.2, SW1.1, U14.17 (~RESET~)
/spindle/FEEDBACK: U14.52 (P2[11]); also elsewhere on the board
/spindle/PWM: U14.37 (P1[23]); also elsewhere on the board
GNDD: C22.2, C23.2, C24.2, C25.2, C26.2, C27.1, C28.1, C29.1, C30.1, C31.1, C32.1, C33.1, J19.1, J21.1, J22.1, J23.4, J23.6, J23.8, J23.10, J23.12, J23.14, J23.16, J23.18, J23.20, J24.1, J25.1, J26.1, J28.1, J29.1, J33.6 (GND), J33.9 (SHIELD), J33.10, J33.11, J34.1, R60.1, SW1.2, SW2.2, U14.11 (VSSA), U14.15 (VREFN), U14.31 (VSS), U14.41 (VSS), U14.55 (VSS), U14.72 (VSS), U14.83 (VSS), U14.97 (VSS); also elsewhere on the board
unnamed: C24.1, U14.22 (XTAL1), Y1.1
unnamed: C25.1, U14.23 (XTAL2), Y1.2
unnamed: C26.1, L1.2, U14.10 (VDDA), U14.12 (VREFP)
unnamed: Q8.3 (D), R59.1

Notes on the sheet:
Programming
One per VDD
I2C
microSD Card
Near SD_CARD
SPI
ETHERNET

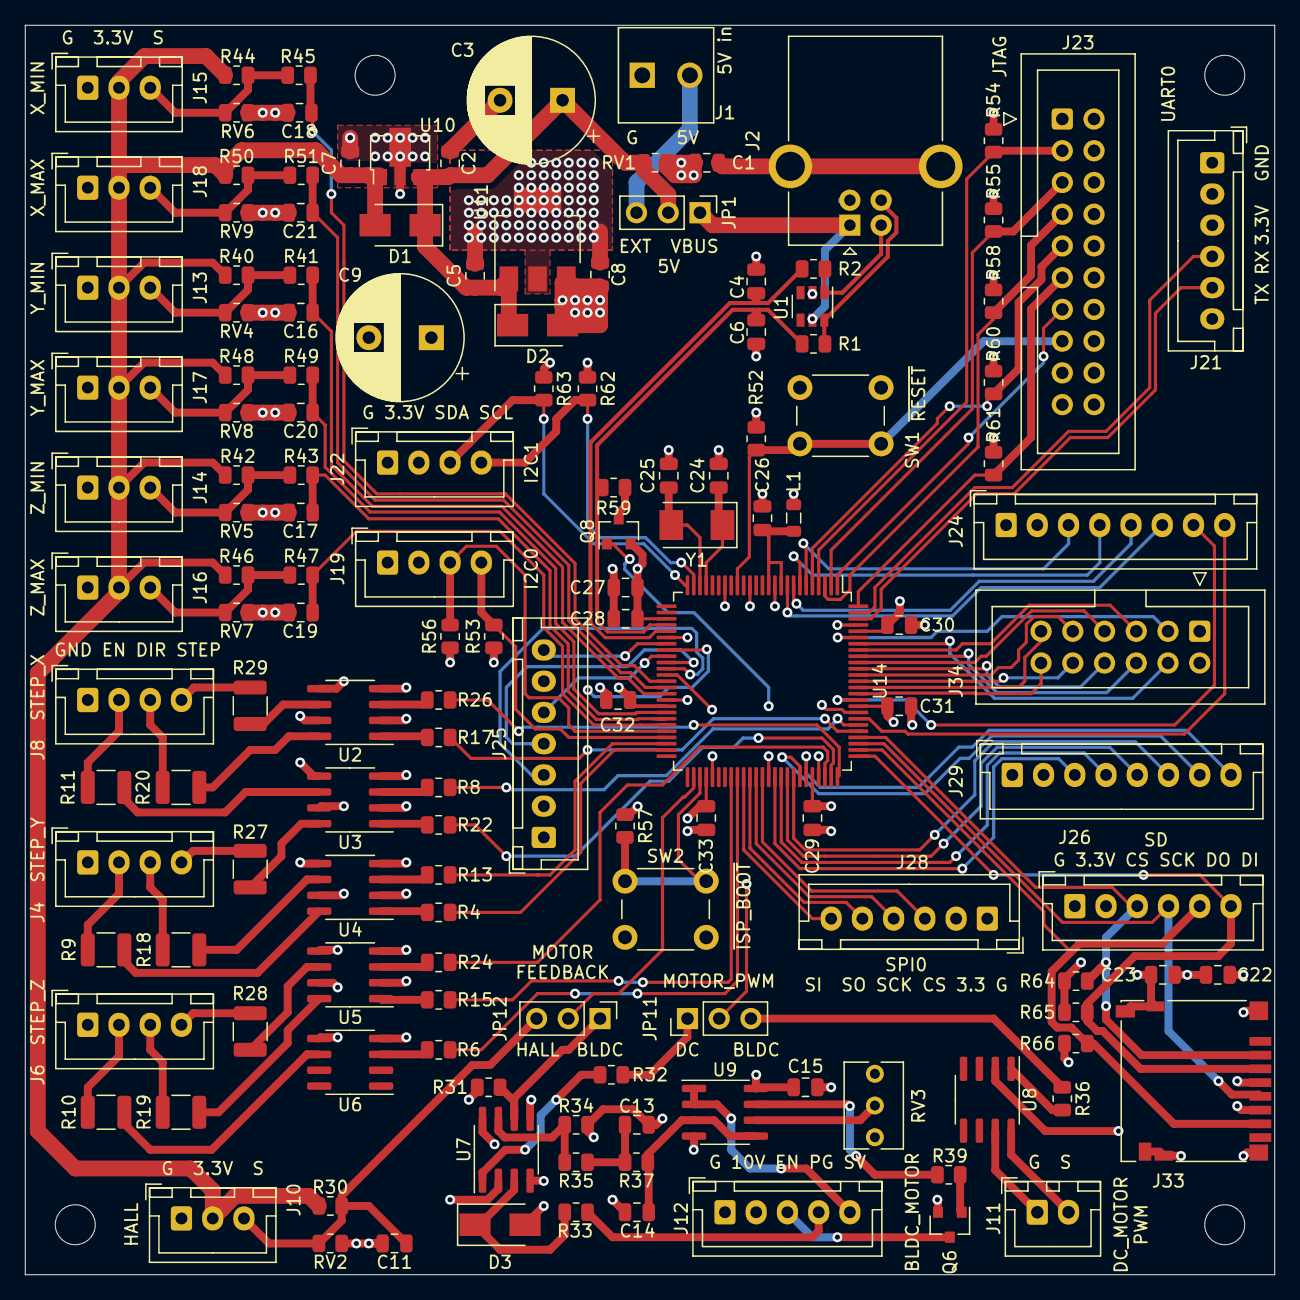
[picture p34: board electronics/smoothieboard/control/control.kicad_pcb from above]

Board: 4 copper layers, 100.0 x 100.0 mm, 145 parts (0 on the bottom side), 138 nets.

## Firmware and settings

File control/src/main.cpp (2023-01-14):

#include "control/Cnc.h"
#include "control/models/SettingsModel.h"
#include "control/models/GCodeModel.h"
#include "control/widgets/MainWindow.h"
#include "control/widgets/SmallMainWindow.h"

#include <QApplication>
#include <QCommandLineParser>

constexpr int SMALL_MAIN_WINDOW_WIDTH = 600;
constexpr int SMALL_MAIN_WINDOW_HEIGHT = 986;

enum class WindowsShowStyle
{
    NORMAL,
    FULLSCREEN,
    MAXIMIZED
};

void messageHandler(QtMsgType type, const QMessageLogContext& context, const QString& msg)
{
    QByteArray localMsg = msg.toLocal8Bit();
    switch (type)
    {
        case QtDebugMsg:
            fprintf(stderr, "Debug: %s\n", localMsg.constData());
            break;
        case QtInfoMsg:
            fprintf(stderr, "Info: %s\n", localMsg.constData());
            break;
        case QtWarningMsg:
            fprintf(stderr, "Warning: %s\n", localMsg.constData());
            break;
        case QtCriticalMsg:
            fprintf(stderr, "Critical: %s\n", localMsg.constData());
            break;
        case QtFatalMsg:
            fprintf(stderr, "Fatal: %s\n", localMsg.constData());
            break;
    }
}

int runApp(bool small, WindowsShowStyle showStyle, bool frameless, bool mockCnc)
{
    qInstallMessageHandler(messageHandler);

    auto settings = SettingsModel::loadOrDefault();
    auto gcodeModel = new GCodeModel;
    Cnc* cnc;
    if (mockCnc)
    {
        cnc = new CncMock(gcodeModel);
    }
    else
    {
        cnc = new SerialPortCnc(gcodeModel);
    }


    QWidget* mainWindow;
    if (small)
    {
        mainWindow = new SmallMainWindow(settings, gcodeModel, cnc);
        if (showStyle == WindowsShowStyle::NORMAL)
        {
            mainWindow->setMinimumSize(SMALL_MAIN_WINDOW_WIDTH, SMALL_MAIN_WINDOW_HEIGHT);
            mainWindow->setMaximumSize(SMALL_MAIN_WINDOW_WIDTH, SMALL_MAIN_WINDOW_HEIGHT);
        }
    }
    else
    {
        mainWindow = new MainWindow(settings, gcodeModel, cnc);
        mainWindow->setMinimumHeight(SMALL_MAIN_WINDOW_HEIGHT);
    }

    mainWindow->setStyleSheet("QWidget {font-size: 13pt;} "
                              "QPushButton {qproperty-iconSize: 20px;} "
                              "QGroupBox {font-weight: bold;} "
                              "QLCDNumber {min-height: 34px;} "
                              "QChartView {padding: 0px; margin: 0px;} "
                              "QSpinBox { border: 1px solid #ABABAB; border-radius: 3px;} "
                              "QSpinBox::up-button {"
                              "  subcontrol-origin: margin;"
                              "  subcontrol-position: center left;"
                              "  left: 1px;"
                              "  height: 24px;"
                              "  width: 32px;"
                              "}"
                              "QSpinBox::down-button {"
                              "  subcontrol-origin: margin;"
                              "  subcontrol-position: center right;"
                              "  right: 1px;"
                              "  height: 24px;"
                              "  width: 32px;"
                              "}");

    if (frameless)
    {
        mainWindow->setWindowFlags(Qt::Window | Qt::FramelessWindowHint);
    }
    switch (showStyle)
    {
        case WindowsShowStyle::FULLSCREEN:
            mainWindow->setWindowState(Qt::WindowFullScreen);
        case WindowsShowStyle::NORMAL:
            mainWindow->show();
            break;
        case WindowsShowStyle::MAXIMIZED:
            mainWindow->showMaximized();
            break;
    }

    int code = QApplication::exec();

    settings->save();
    delete mainWindow;
    delete cnc;
    delete gcodeModel;
    delete settings;

    return code;
}

int main(int argc, char* argv[])
{
    QApplication app(argc, argv);

    QCoreApplication::setOrganizationName("mamaheux");
    QCoreApplication::setOrganizationDomain("mamaheux.com");
    QCoreApplication::setApplicationName("CNC - Control");

    QCommandLineParser parser;
    parser.addHelpOption();
    QCommandLineOption fullscreenOption("fullscreen");
    parser.addOption(fullscreenOption);
    QCommandLineOption maximizedOption("maximized");
    parser.addOption(maximizedOption);
    QCommandLineOption smallOption("small");
    parser.addOption(smallOption);
    QCommandLineOption framelessOption("frameless");
    parser.addOption(framelessOption);
    QCommandLineOption mockCnc("mock_cnc");
    parser.addOption(mockCnc);
    parser.process(app);

    WindowsShowStyle showStyle = WindowsShowStyle::NORMAL;
    if (parser.isSet(fullscreenOption))
    {
        showStyle = WindowsShowStyle::FULLSCREEN;
    }
    else if (parser.isSet(maximizedOption))
    {
        showStyle = WindowsShowStyle::MAXIMIZED;
    }

    return runApp(parser.isSet(smallOption), showStyle, parser.isSet(framelessOption), parser.isSet(mockCnc));
}

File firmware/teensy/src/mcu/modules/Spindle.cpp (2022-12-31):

#include "mcu/modules/Spindle.h"
#include "mcu/utils/InterruptLock.h"
#include "mcu/utils/StringPrint.h"
#include "mcu/criticalError.h"

#include <cnc/modules/ModuleKernel.h>

#include <cstring>

constexpr const char* ENABLE_PIN_KEY = "spindle.enable_pin";
constexpr const char* FEEDBACK_PIN_KEY = "spindle.feedback_pin";
constexpr const char* PWM_PIN_KEY = "spindle.pwm_pin";
constexpr const char* PWM_FREQUENCY_KEY = "spindle.pwm_frequency";

constexpr const char* P_GAIN_KEY = "spindle.control.p";
constexpr const char* I_GAIN_KEY = "spindle.control.i";
constexpr const char* D_GAIN_KEY = "spindle.control.d";
constexpr const char* CONTROL_PERIOD_US_KEY = "spindle.control.period_us";

constexpr const char* RPM_DECAY_KEY = "spindle.rpm.decay";
constexpr const char* PULSE_PER_ROTATION_KEY = "spindle.feedback.pulse_per_rotation";
constexpr const char* MAX_CUMULATIVE_ERROR_KEY = "spindle.max_cumulative_error";

constexpr const char* MISSING_SPINDLE_SPEED_COMMAND_ERROR_MESSAGE = "The spindle speed is missing.";

constexpr uint8_t PIN_INTERRUPT_PRIORITY = 1;

static volatile uint32_t pulseCount = 0;
static volatile uint32_t lastTimeUs = 0;

static void onFeedbackPulse()
{
    constexpr uint32_t MIN_DURATION_US = 500;
    uint32_t currentTimeUs = micros();

    // To prevent pulse cause by noise
    if ((currentTimeUs - lastTimeUs) > MIN_DURATION_US)
    {
        pulseCount++;
    }
    lastTimeUs = currentTimeUs;
}

FLASHMEM Spindle::Spindle()
    : m_lastPulseCount(0),
      m_cumulativeError(0.f),
      m_previousError(0.f),
      m_currentRpm(0.f),
      m_targetRpm(0.f)
{
    memset(m_response, '\0', MAX_SPINDLE_RESPONSE_SIZE);
}

FLASHMEM void Spindle::configure(const ConfigItem& item)
{
    if (strcmp(item.getKey(), ENABLE_PIN_KEY) == 0)
    {
        m_enableConfig = DigitalOutputConfig::parse(item.getValueString());
    }
    else if (strcmp(item.getKey(), FEEDBACK_PIN_KEY) == 0)
    {
        m_feedbackConfig = DigitalInputConfig::parse(item.getValueString());
    }
    else if (strcmp(item.getKey(), PWM_PIN_KEY) == 0)
    {
        if (m_pwmConfig.has_value())
        {
            m_pwmConfig = PwmOutputConfig::parse(item.getValueString(), m_pwmConfig->frequency());
        }
        else
        {
            m_pwmConfig = PwmOutputConfig::parse(item.getValueString(), 0);
        }
    }
    else if (strcmp(item.getKey(), PWM_FREQUENCY_KEY) == 0)
    {
        if (m_pwmConfig.has_value())
        {
            m_pwmConfig = PwmOutputConfig(m_pwmConfig->pin(), m_pwmConfig->inverted(), item.getValueFloat());
        }
        else
        {
            m_pwmConfig = PwmOutputConfig(0, false, item.getValueFloat());
        }
    }
    else if (strcmp(item.getKey(), P_GAIN_KEY) == 0)
    {
        m_p = item.getValueFloat();
    }
    else if (strcmp(item.getKey(), I_GAIN_KEY) == 0)
    {
        m_i = item.getValueFloat();
    }
    else if (strcmp(item.getKey(), D_GAIN_KEY) == 0)
    {
        m_d = item.getValueFloat();
    }
    else if (strcmp(item.getKey(), CONTROL_PERIOD_US_KEY) == 0)
    {
        m_controlPeriodUs = item.getValueInt();
    }
    else if (strcmp(item.getKey(), RPM_DECAY_KEY) == 0)
    {
        m_rpmDecay = item.getValueFloat();
    }
    else if (strcmp(item.getKey(), PULSE_PER_ROTATION_KEY) == 0)
    {
        m_pulsePerRotation = item.getValueFloat();
    }
    else if (strcmp(item.getKey(), MAX_CUMULATIVE_ERROR_KEY) == 0)
    {
        m_maxCumulativeError = item.getValueFloat();
    }
}

FLASHMEM void Spindle::checkConfigErrors(const MissingConfigCallback& onMissingConfigItem)
{
    CHECK_CONFIG_ERROR(onMissingConfigItem, m_enableConfig.has_value(), ENABLE_PIN_KEY);
    CHECK_CONFIG_ERROR(onMissingConfigItem, m_feedbackConfig.has_value(), FEEDBACK_PIN_KEY);
    CHECK_CONFIG_ERROR(onMissingConfigItem, m_pwmConfig.has_value(), PWM_PIN_KEY);
    CHECK_CONFIG_ERROR(onMissingConfigItem, m_p.has_value(), P_GAIN_KEY);
    CHECK_CONFIG_ERROR(onMissingConfigItem, m_i.has_value(), I_GAIN_KEY);
    CHECK_CONFIG_ERROR(onMissingConfigItem, m_d.has_value(), D_GAIN_KEY);
    CHECK_CONFIG_ERROR(onMissingConfigItem, m_controlPeriodUs.has_value(), CONTROL_PERIOD_US_KEY);
    CHECK_CONFIG_ERROR(onMissingConfigItem, m_rpmDecay.has_value(), RPM_DECAY_KEY);
    CHECK_CONFIG_ERROR(onMissingConfigItem, m_pulsePerRotation.has_value(), PULSE_PER_ROTATION_KEY);
    CHECK_CONFIG_ERROR(onMissingConfigItem, m_maxCumulativeError.has_value(), MAX_CUMULATIVE_ERROR_KEY);
}

FLASHMEM void Spindle::begin()
{
    m_enable.begin(*m_enableConfig, false);
    m_feedback.begin(*m_feedbackConfig);
    DigitalInput::setInterruptPriority(PIN_INTERRUPT_PRIORITY);
    m_feedback.attachInterrupt(&onFeedbackPulse, DigitalInputInterruptMode::INTERRUPT_CHANGE);
    m_pwm.begin(*m_pwmConfig, 0);

    setUpdatePeriodUs(*m_controlPeriodUs);
    m_kernel->registerToEvent(ModuleEventType::MCODE_COMMAND, this);
}
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

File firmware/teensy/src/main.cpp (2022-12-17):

#include "config.h"
#include "mcu/criticalError.h"

#include "mcu/modules/Kernel.h"
#include "mcu/modules/FileSystem.h"
#include "mcu/modules/CommandSerial.h"
#include "mcu/modules/CommandFile.h"
#include "mcu/modules/Planner.h"
#include "mcu/modules/StepperController.h"
#include "mcu/modules/Endstops.h"
#include "mcu/modules/Spindle.h"
#include "mcu/modules/LinearBlockExecutor.h"

#include <cnc/modules/CoordinateTransformer.h>
#include <cnc/modules/ArcConverter.h>

#include <SD.h>

FileSystem fileSystem;
CommandSerial commandSerial;
CommandFile commandFile;

CoordinateTransformer coordinateTransformer;
ArcConverter arcConverter(&coordinateTransformer);
Planner planner(&coordinateTransformer, &arcConverter);

StepperController stepperController(&coordinateTransformer, &planner);
Endstops endstops(&planner, &stepperController);
Spindle spindle;
LinearBlockExecutor linearBlockExecutor(&stepperController, &spindle, &planner);

Kernel kernel;

FLASHMEM void setupKernel()
{
    DEBUG_SERIAL.println("Setup the kernel");

    kernel.addModule(&fileSystem);
    kernel.addModule(&commandSerial);
    kernel.addModule(&commandFile);

    kernel.addModule(&coordinateTransformer);
    kernel.addModule(&arcConverter);
    kernel.addModule(&planner);

    kernel.addModule(&endstops);
    kernel.addModule(&stepperController);
    kernel.addModule(&spindle);
    kernel.addModule(&linearBlockExecutor);
    kernel.begin();
}

FLASHMEM void setup()
{
    DEBUG_SERIAL.begin(DEBUG_SERIAL_BAUD_RATE);
    setupCriticalErrorCheck();
    SD.begin(BUILTIN_SDCARD);

    setupKernel();
}

void loop()
{
    kernel.update();
}

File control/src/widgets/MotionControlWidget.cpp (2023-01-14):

#include "control/widgets/MotionControlWidget.h"

#include <QHBoxLayout>
#include <QVBoxLayout>
#include <QGridLayout>
#include <QStyle>

constexpr int MINIMUM_SPEED_FACTOR = 10;
constexpr int MAXIMUM_SPEED_FACTOR = 200;
constexpr int DEFAULT_SPEED_FACTOR = 100;
constexpr int SPEED_FACTOR_STEP = 5;

MotionControlWidget::MotionControlWidget(SettingsModel* settings, Cnc* cnc, QWidget* parent)
    : QWidget(parent),
      m_state(State::STEPPERS_DISABLED),
      m_cnc(cnc)
{
    createUi(settings);
    onSpeedFactorSliderValueChanged(DEFAULT_SPEED_FACTOR);

    connect(settings, &SettingsModel::settingsChanged, this, &MotionControlWidget::onSettingsChanged);
    connect(m_cnc, &Cnc::cncConnected, this, &MotionControlWidget::onCncConnected);
    connect(m_cnc, &Cnc::cncDisconnected, this, &MotionControlWidget::onCncDisconnected);
    connect(m_cnc, &Cnc::stepperStateChanged, this, &MotionControlWidget::onStepperStateChanged);

    connect(m_cnc, &Cnc::gcodeFileStated, this, &MotionControlWidget::disableMotionWidgets);
    connect(m_cnc, &Cnc::gcodeFileAborted, this, &MotionControlWidget::enableMotionWidgets);
    connect(m_cnc, &Cnc::gcodeFileFinished, this, &MotionControlWidget::enableMotionWidgets);

    onCncDisconnected();
}

void MotionControlWidget::onCncConnected()
{
    setEnabled(true);
    m_cnc->disableSteppers();
    setState(State::STEPPERS_DISABLED);
    enableMotionWidgets();
}

void MotionControlWidget::onCncDisconnected()
{
    setEnabled(false);
}

void MotionControlWidget::onStepperStateChanged(bool isEnabled)
{
    if (isEnabled)
    {
        setState(State::STEPPERS_ENABLED);
    }
    else
    {
        setState(State::STEPPERS_DISABLED);
    }
}

void MotionControlWidget::onEnableSteppersButtonPressed()
{
    m_cnc->enableSteppers();
}

void MotionControlWidget::onDisableSteppersButtonPressed()
{
    m_cnc->disableSteppers();
}

void MotionControlWidget::onGotoMachineX0Y0ButtonPressed()
{
    m_cnc->gotoMachineX0Y0(m_feedRateSpinBox->value());
}

void MotionControlWidget::onGotoWorkX0Y0ButtonPressed()
{
    m_cnc->gotoWorkX0Y0(m_feedRateSpinBox->value());
}

void MotionControlWidget::onXBackwardButtonPressed()
{
    m_cnc->jogX(-static_cast<float>(m_distanceButtonGroup->checkedId()) / 10.f, m_feedRateSpinBox->value());
}

void MotionControlWidget::onXForwardButtonPressed()
{
    m_cnc->jogX(static_cast<float>(m_distanceButtonGroup->checkedId()) / 10.f, m_feedRateSpinBox->value());
}

void MotionControlWidget::onYBackwardButtonPressed()
{
    m_cnc->jogY(-static_cast<float>(m_distanceButtonGroup->checkedId()) / 10.f, m_feedRateSpinBox->value());
}

void MotionControlWidget::onYForwardButtonPressed()
{
    m_cnc->jogY(static_cast<float>(m_distanceButtonGroup->checkedId()) / 10.f, m_feedRateSpinBox->value());
}

void MotionControlWidget::onZBackwardButtonPressed()
{
    m_cnc->jogZ(-static_cast<float>(m_distanceButtonGroup->checkedId()) / 10.f, m_feedRateSpinBox->value());
}

void MotionControlWidget::onZForwardButtonPressed()
{
    m_cnc->jogZ(static_cast<float>(m_distanceButtonGroup->checkedId()) / 10.f, m_feedRateSpinBox->value());
}

void MotionControlWidget::onSpeedFactorSliderValueChanged(int value)
{
    m_speedFactorLabel->setText(QString::number(value) + "%");
    m_cnc->setSpeedFactor(value);
}

void MotionControlWidget::onResetSpeedFactorButtonPressed()
{
    m_speedFactorSlider->setValue(DEFAULT_SPEED_FACTOR);
}

void MotionControlWidget::onSettingsChanged(const SettingsModel& settings)
{
    m_feedRateSpinBox->setRange(settings.minimumFeedRateInMmPerMin(), settings.maximumFeedRateInMmPerMin());
}

void MotionControlWidget::enableMotionWidgets()
{
    setState(m_state);

    m_gotoMachineX0Y0Button->setEnabled(true);
    m_gotoWorkX0Y0Button->setEnabled(true);

    m_xBackwardButton->setEnabled(true);
    m_xForwardButton->setEnabled(true);
    m_yBackwardButton->setEnabled(true);
    m_yForwardButton->setEnabled(true);
    m_zBackwardButton->setEnabled(true);
    m_zForwardButton->setEnabled(true);

    m_01DistanceButton->setEnabled(true);
    m_1DistanceButton->setEnabled(true);
    m_10DistanceButton->setEnabled(true);
    m_100DistanceButton->setEnabled(true);

    m_feedRateSpinBox->setEnabled(true);
}

void MotionControlWidget::disableMotionWidgets()
{
    m_enableSteppersButton->setEnabled(false);
    m_disableSteppersButton->setEnabled(false);

    m_gotoMachineX0Y0Button->setEnabled(false);
    m_gotoWorkX0Y0Button->setEnabled(false);

    m_xBackwardButton->setEnabled(false);
    m_xForwardButton->setEnabled(false);
    m_yBackwardButton->setEnabled(false);
    m_yForwardButton->setEnabled(false);
    m_zBackwardButton->setEnabled(false);
    m_zForwardButton->setEnabled(false);

    m_01DistanceButton->setEnabled(false);
    m_1DistanceButton->setEnabled(false);
    m_10DistanceButton->setEnabled(false);
    m_100DistanceButton->setEnabled(false);

    m_feedRateSpinBox->setEnabled(false);
}

void MotionControlWidget::setState(State state)
{
    m_state = state;
    switch (m_state)
    {
        case State::STEPPERS_ENABLED:
            m_enableSteppersButton->setEnabled(false);
            m_disableSteppersButton->setEnabled(true);
            break;
        case State::STEPPERS_DISABLED:
            m_enableSteppersButton->setEnabled(true);
            m_disableSteppersButton->setEnabled(false);
            break;
    }
}
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

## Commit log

2021-04-06 Add CAD files.
    [2020x600mm.SLDPRT, 2080x130mm.SLDPRT, 2080x270mm.SLDPRT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]
2021-04-08 Add the controller schematic.
    [control.kicad_pcb, control.sch, endstops.sch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]
2021-04-09 Add the PCB.
    [BOM.ods, control.sch, endstops.sch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]
2021-10-26 Add the teensy control board
    [BOM.ods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]
2021-10-27 Add core classes and functions.
    [control.kicad_pcb]
2021-10-27 Add ResourceLock tests.
    [BOM.ods, control.kicad_pcb, mcu.sch]
2021-11-03 Add gerber files
    [control-B_Cu.gbl, control-B_Mask.gbs, control-B_Paste.gbp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]
2021-11-08 Add CoordinateTransformer (tests are missing).
    [main.cpp]
2021-11-08 Add Stepper
2021-11-08 Add Spindle
2021-11-14 Add BoundedQueue. Add error messages.
    [Spindle.cpp, main.cpp]
2021-11-15 Refactor steppers. Add Stepper Controller. Add Vector2. Add Vector3. Add FixedPoint. Add ArcConverter (tests are missing).
    [Spindle.cpp, main.cpp]
2021-11-16 Add a missing test (ArcConverter G53)
    [main.cpp]
2022-11-23 Fix G92. Add Planer, Endstops, ... class skeletons.
    [Spindle.cpp]
2022-11-28 Fix viewing G2 and G3. Improve GCode parsing.
    [Cnc.cpp, MotionControlWidget.cpp]
2022-11-28 Fix error messages. Add the command queue.
    [Cnc.cpp, MainWindow.cpp]
2022-12-01 Fix arc problems. Add start and stop gcode file.
    [Cnc.cpp]
2022-12-03 Add a shutdown button
2022-12-04 Fix spindle PID
2022-12-05 Disable buttons when the gcode file is started.
2022-12-05 Add LinearBlockExecutor. Finalize Endstops.
2022-12-07 Update spindle support
    [2080x270mm.SLDPRT, 2080x630mm.SLDPRT, BF12.SLDPRT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]
2022-12-08 Fix ArcConverter. Add tests. Format.
    [Spindle.cpp, main.cpp]
2022-12-08 Fix gcode model. Update the app style.
    [MotionControlWidget.cpp, SettingsDialog.cpp, SpindleControlWidget.cpp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]
2022-12-10 Fix Cnc classes. Add icons
    [Cnc.cpp, MainWindow.cpp, SmallMainWindow.cpp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]
2022-12-10 Connect console enter to the send button.^C
2022-12-18 Fix DigitalInput::attachInterrupt
2023-01-07 Fix Z frame rigidity
    [CNC.SLDASM, Y frame screw support.SLDPRT, Z frame support bottom.SLDPRT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]
2023-01-19 Fix imperial feedrates. Add estimated duration in the control.
    [SpindleControlWidget.cpp]
2023-04-05 Fix firmware and control
    [Cnc.cpp]
2024-12-30 Update the config for the closed loop steppers.
2024-12-30 Fix endstops period.
